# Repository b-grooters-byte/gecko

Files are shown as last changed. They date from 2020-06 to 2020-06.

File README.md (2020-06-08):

# Gecko
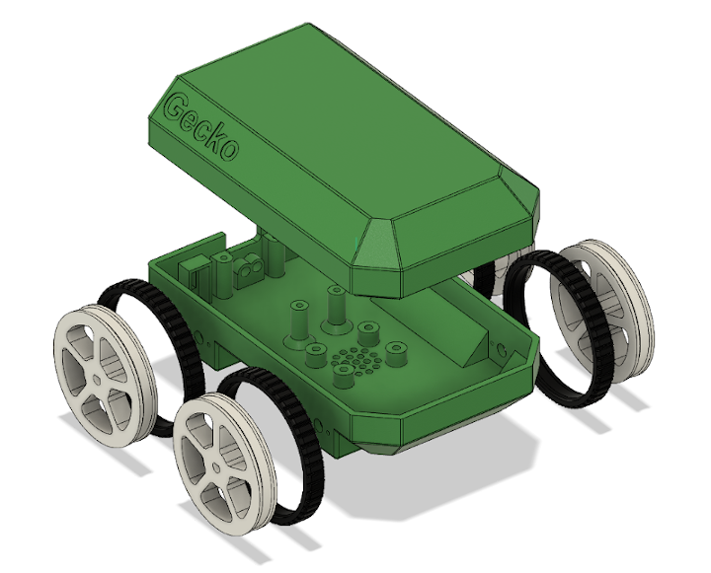
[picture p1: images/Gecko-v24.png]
Exploded View


Gecko is a small Arduino Mini based 4 wheel rover. It is designed for BLE 
control utilizing the TrailBlazer iOS app although any iOS or Arduino 
Bluetooth rover control app would work with different on-board controller 
software. This bot does not include a sensor suite as it is intended to be 
a relatively simple starter project for building and understanding a BLE 
controlled bot.

Gecko will run well on tile or wood floors but may struggle on thicker carpet 
due to the small size and low chassis clearance. Gecko utilizes differential 
steering which creates an additional challenge on carpets or rugs.

Gecko utilizes an AdaFruit USB charging board and 2500mAh LiPo battery so that 
you can recharge and run without opening the chassis or disconnecting any wiring. 
LiPo batteries can be dangerous so please follow all recommended safety precautions
when with working with them.

In this repository you will find the STL files and Gecko on-board Arduino sketch.

## Controller
The [controller sketch](sketch/Controller.md) is a relatively simple motor command
controller that reads input from the HM-10 module on serial input.

## Components
The total cost for the components as built is around $107USD. Gecko can be
built for a lower cost by excluding the PowerBoost 1000 ($24USD) or substituting it with the 
PowerBoost 500 although the prototype does have the 1000 installed.

* [N20 Micro 150RPM 6V DC Motor](https://www.amazon.com/gp/product/B07R52WG9J/)
* [Arduino Pro Mini 5V 16MHz](https://www.amazon.com/HiLetgo-Atmega328P-AU-Development-Microcontroller-Bootloadered/dp/B00E87VWQW/)
* [AdaFruit PowerBoost 1000](https://www.amazon.com/gp/product/B01BMRBTH2)
* [2500 mAh 3.7V Battery](https://www.amazon.com/2500mAh-battery-Rechargeable-Lithium-Connector/dp/B07BTR3BZ4/) 
* [HM-10 BLE Module](https://www.amazon.com/gp/product/B06WGZB2N4)
* [L9110S DC Motor Controller](https://www.amazon.com/gp/product/B00M0F243E/)
* [SPDT 3 Pin Switch](https://www.amazon.com/gp/product/B01N7NCW8N)
* [3mm Green LED](https://www.amazon.com/JABINCO-Circuit-Assorted-Science-Experiment/dp/B0827KYRFH)
* [3mm Red or Yellow LED](https://www.amazon.com/JABINCO-Circuit-Assorted-Science-Experiment/dp/B0827KYRFH)

## Additional Part and Tools
* [Angled Header Pins](https://www.amazon.com/Antrader-2-54mm-Right-Header-Connector/dp/B07M88GRHG)
* [26AWG Wire](https://www.amazon.com/Stranded-Felexible-Insulated-Electronic-ELectrical/dp/B07J3DS831)
* Heat Shrink Tubing
* M1.4x4 Screws
* M2 Screws
* M2.5 Screws
* PLA
* TPU
* Soldering Iron

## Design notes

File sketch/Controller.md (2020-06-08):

# Controller

The controller for Gecko is a very simple controller for Bluetooth Low Energy 
(BLE) and the L9110S controller. It is set up to command 4 motors with 2 left 
and 2 right. It enables control of the speed and direction with enough fidelity
for smooth acceleration and deceleration. 

There were several requirements that went into controller design.

* I have found that the motors do not respond to the full range of possible values from
0 - 255 although I wanted more control than STOP-SLOW-MED-FAST that some BLE controllers
provide. 

* Gecko uses the HM-10 BLE module which I have found will drop data at any transmission
rate. This may not be common to all HM-10 modules; however, to avoid any code complexity
around error handling I wanted a simple command channel.

* The TrailBlazer iOS App includes a controller designed for single thumb control
for speed and direction that simulates analog joystick like input. The onboard
controller should support this.

These requirements led to a single byte command for motor speed and direction that 
allow relatively fine grained controll of the motors with a command channel that 
responds will to dropped bytes and a continuous stream of command data from the 
remote controller application.

## Motor Command

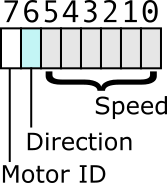
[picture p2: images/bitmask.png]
Motor Command


The motor command for left and right motors is a simple single byte command. 
* bit 7 is the motor ID
* bit 6 is the motor direction 
* bit 5-0 are the motor speed

The controller uses simple bit masks and shift operators to decode the command.

    motor_id = command & 0x80;
    direction = command & 0x40;
    speed = (command & 0x3F) << 2;
 
The parenthesis around (command & 0x3F) are  necessary since the bitwide AND, `&` 
operator has a lower precedence than the bitwise shift left `<<` operator. There are 
references below if you are unfamiliar with the C bitwise operators: 

* [C Operator Precedence](https://en.cppreference.com/w/c/language/operator_precedence)
* [C Bitwise Operators](https://www.programiz.com/c-programming/bitwise-operators)

These bit mask values are replaced with preprocessor defines in the code:

    //-----------------------------------------------------------------------------
    // Command bit masks
    #define INPUT_MASK_MOTOR    0x80
    #define INPUT_MASK_DIR      0x40
    #define INPUT_MASK_SPEED    0x3F

The controller includes a function that sends the commands to the L9110S

    static void motor_command(uint8_t motor_id, uint8_t speed, uint8_t direction) {
     ...
    }

This makes the main loop a simple serial read to get the next byte from the HM-10, 
decode it and send it to the motors. The controller code is simple since each command
is atomic and there is no sequence of bytes that have to be read.

    void loop() {
        // wait for input
        while( !Serial.available() ); 
        input = Serial.read();
        // get the motor ID
        motor_id = (input & INPUT_MASK_MOTOR) == 0 ? MOTOR_LEFT : MOTOR_RIGHT;    
        // get the motor direction
        direction = (input & INPUT_MASK_DIR) == 0 ? DIR_FORWARD : DIR_REVERSE;
        // get the motor speed
        speed = (input & INPUT_MASK_SPEED) << 2;
        motor_command(motor_id, speed, direction);
    }

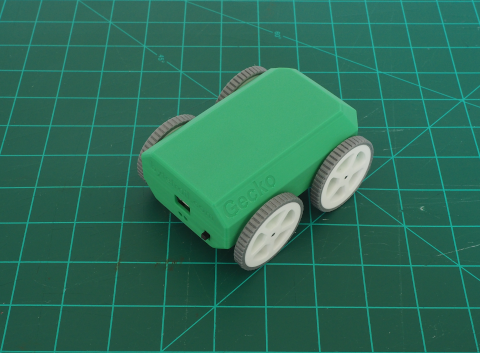
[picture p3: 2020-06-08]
images/chassis-right-rear-sm.png

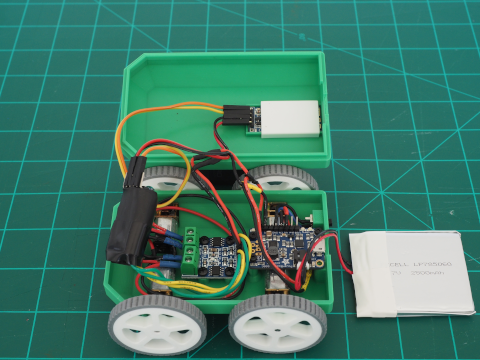
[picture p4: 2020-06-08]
images/chassis-open-01-sm.png

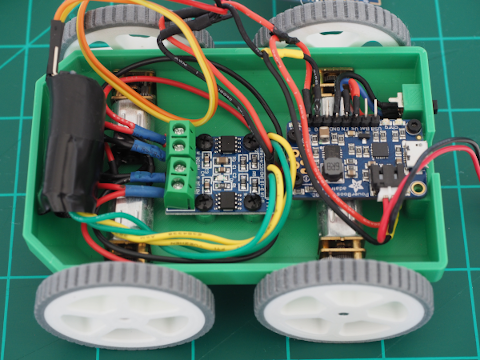
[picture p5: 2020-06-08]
images/chassis-open-02-sm.png

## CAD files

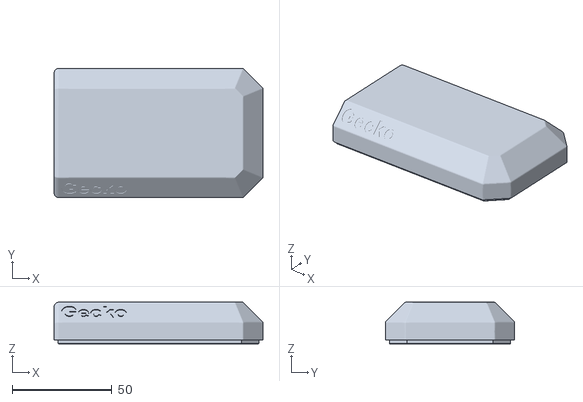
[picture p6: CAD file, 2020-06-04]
stl/gecko-chassis-upper.stl
105.0 x 65.0 x 21.0

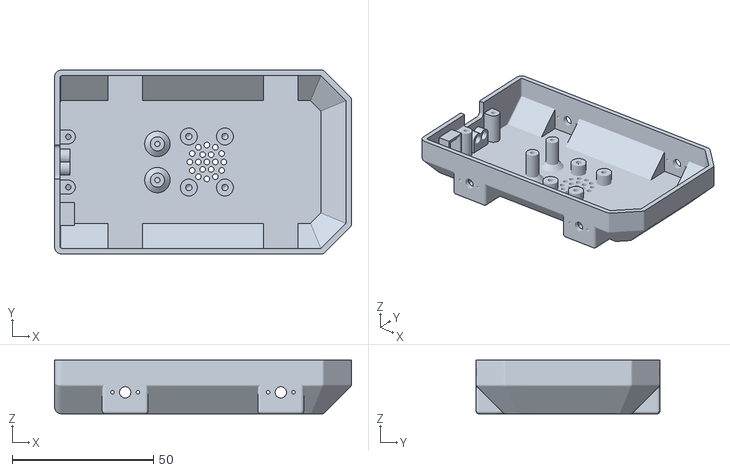
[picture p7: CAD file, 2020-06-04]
stl/gecko-chassis-lower.stl
105.0 x 65.0 x 19.0

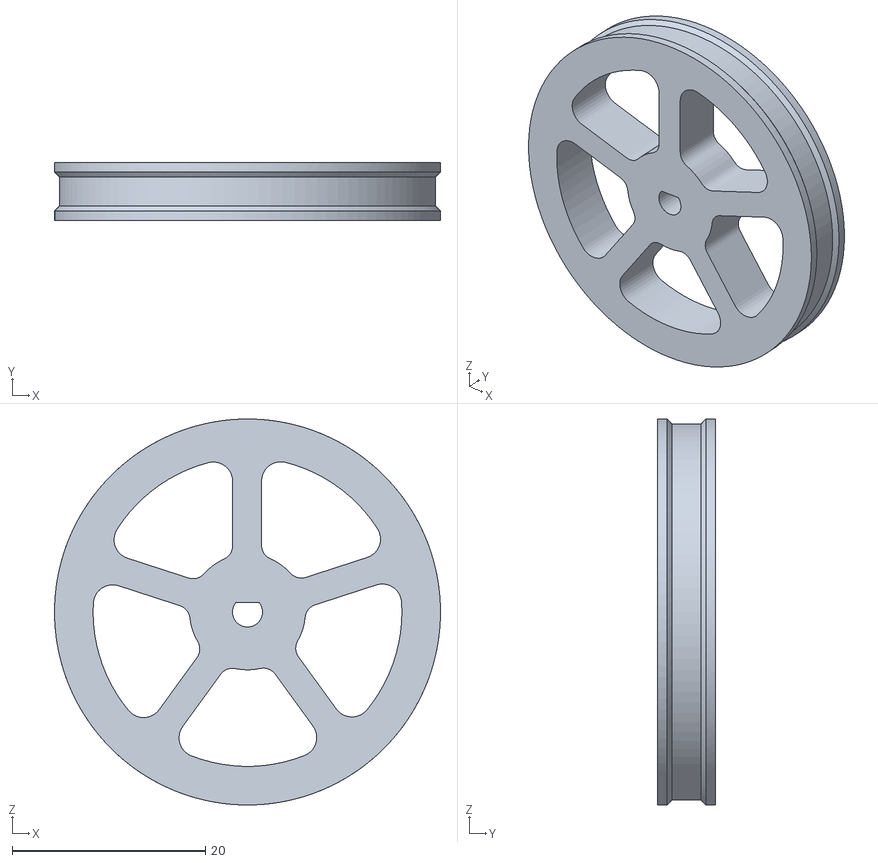
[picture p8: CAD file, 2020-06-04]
stl/gecko-wheel.stl
40.0 x 6.00 x 40.0

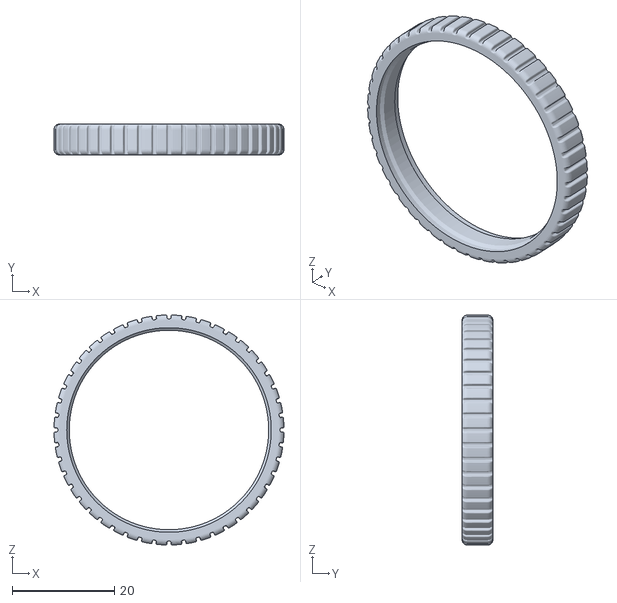
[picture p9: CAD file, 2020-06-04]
stl/gecko-tire.stl
45.0 x 6.00 x 45.0

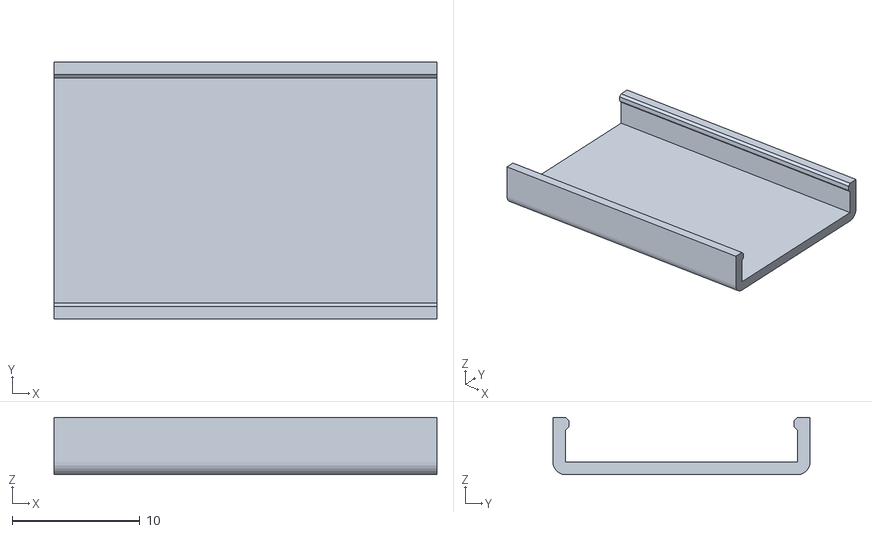
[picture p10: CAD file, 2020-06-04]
stl/gecko-ble-cover.stl
30.0 x 20.2 x 4.50

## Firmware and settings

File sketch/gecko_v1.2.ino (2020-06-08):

/*
 *  Gecko v1.2 Arduino Sketch
 *  Copyright 2020, ByteTrail, LLC 
 *  
 * Licensed under the Apache License, Version 2.0 (the "License");
 * you may not use this file except in compliance with the License.
 * You may obtain a copy of the License at
 *
 *   http://www.apache.org/licenses/LICENSE-2.0
 *
 * Unless required by applicable law or agreed to in writing, software
 * distributed under the License is distributed on an "AS IS" BASIS,
 * WITHOUT WARRANTIES OR CONDITIONS OF ANY KIND, either express or implied.
 * See the License for the specific language governing permissions and
 * limitations under the License.
 *  
 */
 
//-----------------------------------------------------------------------------
// Pin IO definitions
#define MOTOR_A_PWM  5    // 9110 left motor speed
#define MOTOR_A_DIR  3    // 9110 left motor direction
#define MOTOR_B_PWM  6    // 9110 right motor speed
#define MOTOR_B_DIR  4    // 9110 right motor direction

#define MOTOR_LEFT     0  // pin offsets for left motor
#define MOTOR_RIGHT    1  // pin offsets for right motor
#define PWM_OFFSET     5  // pin offset for motor PWM pin
#define DIR_OFFSET     3  // pin offset for motor direction pin

//-----------------------------------------------------------------------------
// Gecko controller definitions
#define SPEED_MAX           0xFF
#define DIR_FORWARD         HIGH
#define DIR_REVERSE         LOW

//-----------------------------------------------------------------------------
// Command bit masks
#define INPUT_MASK_MOTOR    0x80
#define INPUT_MASK_DIR      0x40
#define INPUT_MASK_SPEED    0x3F

//-----------------------------------------------------------------------------
// function declarations
static void motor_command(uint8_t motor_id, uint8_t speed, uint8_t direction);


uint8_t input = 0;
uint8_t speed = 0;
uint8_t direction = 0;
uint8_t motor_id = 0;

void setup() {
  // left motor
  pinMode( MOTOR_A_DIR, OUTPUT );
  pinMode( MOTOR_A_PWM, OUTPUT );
  digitalWrite( MOTOR_A_DIR, LOW );
  digitalWrite( MOTOR_A_PWM, LOW );
  // right motor
  pinMode( MOTOR_B_DIR, OUTPUT );
  pinMode( MOTOR_B_PWM, OUTPUT );
  digitalWrite( MOTOR_B_DIR, LOW );
  digitalWrite( MOTOR_B_PWM, LOW );
  
  Serial.begin( 9600 );
}

/*!
 *  \brief primary loop
 *  
 *  The Gecko main loop will wait for data to be available on the serial
 *  connection. Each byte read is treated as a motor command. No error 
 *  checking is completed prior to attempting to command the motor.
 */
void loop() {
    while( !Serial.available() ) ; // wait for input
    input = Serial.read();
    motor_id = (input & INPUT_MASK_MOTOR) == 0 ? MOTOR_LEFT : MOTOR_RIGHT;    
    direction = (input & INPUT_MASK_DIR) == 0 ? DIR_FORWARD : DIR_REVERSE;
    speed = (input & INPUT_MASK_SPEED) << 2;
    motor_command(motor_id, speed, direction);
}

/*!
 * \brief Sends a command to a motor
 * 
 *  This function sends a speed and direction command to the motor controller. 
 *  4 motors are connected to the L9110S so either the 2 LEFT or 2 RIGHT motors 
 *  are receiving the command.
 *  
 * \param motor_id The motor identifier: MOTOR_LEFT or MOTOR_RIGHT 
 * \param speed The speed to set. This is a value between 0 and 255 although in practice
 *              a range of ~=50 - ~= 200 is applicable to the N20 motors used
 * \param direction DIR_FORWARD or DIR_REVERSE
 */
static void motor_command(uint8_t motor_id, uint8_t speed, uint8_t direction) {
  // simple error check on motor ID
  if( motor_id > 1 ) {
    return;
  }
  // set the motor speed and direction
  if ( direction == DIR_FORWARD ) {
    speed = SPEED_MAX - speed;
  }
  digitalWrite( motor_id + DIR_OFFSET, direction );       
  analogWrite( motor_id + PWM_OFFSET, speed );   
}


 
